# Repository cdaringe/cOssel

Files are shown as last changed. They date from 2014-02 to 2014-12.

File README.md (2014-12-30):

# cOssel
cOssel is a 3D printer.
cOssel makes stuff.
cOssel is big.
cOssel is neat.
cOssel is an iteration of Johann's Kossel. Design intents are equip a dual head end effector and to move the linear rails to an open design. It also uses 20x20 instead of Kossel's 15x15.  Various other design constructs are changed, however, the core design intent of the printer remains.  Default setup includes support for Dual Extruders, heated bed, and EE fan.

## Docs
Please visit the RepRap wiki for docs: http://reprap.org/wiki/COssel

Find printable (RP) files in the /stl folder.  Plates are available in the /stl/plates folder.
Find the official BOM in the root, cossel_BOM.xlsm file.

Adios!  Enjoy!

http://cdaringe.net/

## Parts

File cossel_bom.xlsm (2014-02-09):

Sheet: ExplodedBOM
QtyScalar | ParentLine | . | BOM Level | Part | Qty | UOM | Qty_Exploded | Vendor | Phantom
1 | 1 |  | 0 | (SUPERBOM) | 1 | ea | 1 |  | TRUE
1 | 2 |  | 1 | (post) | 3 | ea | 3 |  | TRUE
3 | 3 |  | 2 | 2020-800mm | 1 | ea | 3 |  | FALSE
3 | 3 |  | 2 | open_rail-700mm | 1 | ea | 3 |  | FALSE
3 | 3 |  | 2 | scrw_m5_10 (open_rail_kit_excess) | 15 | ea | 45 |  | FALSE
3 | 3 |  | 2 | nut_extr_m5 (open_rail_kit_excess) | 15 | ea | 45 |  | FALSE
3 | 3 |  | 2 | rp_base_vertex | 1 | ea | 3 |  | FALSE
3 | 3 |  | 2 | motor_nema_17 | 1 | ea | 3 |  | FALSE
3 | 3 |  | 2 | belt_gt2_1700mm | 1 | ea | 3 |  | FALSE
3 | 3 |  | 2 | gear_drive_belt_gt2 | 1 | ea | 3 |  | FALSE
3 | 3 |  | 2 | scrw_m3_set | 1 | ea | 3 |  | FALSE
3 | 3 |  | 2 | 2020-300mm | 2 | ea | 6 |  | FALSE
3 | 3 |  | 2 | scrw_m4_10 | 8 | ea | 24 |  | FALSE
3 | 3 |  | 2 | wshr_m4 | 10 | ea | 30 |  | FALSE
3 | 3 |  | 2 | nut_m4_extr | 10 | ea | 30 |  | FALSE
3 | 3 |  | 2 | scrw_m3_12 | 4 | ea | 12 |  | FALSE
3 | 3 |  | 2 | wshr_m3 | 4 | ea | 12 |  | FALSE
3 | 3 |  | 2 | scrw_m4_12 | 2 | ea | 6 |  | FALSE
3 | 3 |  | 2 | (carriage) | 1 | ea | 3 |  | TRUE
3 | 20 |  | 3 | rp_plate_slider | 1 | ea | 3 |  | FALSE
3 | 20 |  | 3 | open_rail_shim | 2 | ea | 6 |  | FALSE
3 | 20 |  | 3 | open_rail_wheel_delrin | 2 | ea | 6 |  | FALSE
3 | 20 |  | 3 | open_rail_wheel_sst | 2 | ea | 6 |  | FALSE
3 | 20 |  | 3 | open_rail_bearing | 8 | ea | 24 |  | FALSE
3 | 20 |  | 3 | open_rail_spacer_bearing | 4 | ea | 12 |  | FALSE
3 | 20 |  | 3 | open_rail_shim_eccentric | 2 | ea | 6 |  | FALSE
3 | 20 |  | 3 | open_rail_scrw_m5_std_wheel_mnt | 4 | ea | 12 |  | FALSE
3 | 20 |  | 3 | open_rail_nut_m5 | 4 | ea | 12 |  | FALSE
3 | 20 |  | 3 | rp_flag_carriage | 1 | ea | 3 |  | FALSE
3 | 20 |  | 3 | nut_m3_jam | 3 | ea | 9 |  | FALSE
3 | 20 |  | 3 | wshr_m3 | 3 | ea | 9 |  | FALSE
3 | 20 |  | 3 | nut_m3 | 3 | ea | 9 |  | FALSE
3 | 20 |  | 3 | scrw_m3_20 | 2 | ea | 6 |  | FALSE
1 | 2 |  | 1 | (rods) | 6 | ea | 6 |  | TRUE
6 | 35 |  | 2 | rod_carbon_330mm | 1 | ea | 6 |  | FALSE
6 | 35 |  | 2 | rod_ends | 2 | ea | 12 | klj | FALSE
6 | 35 |  | 2 | scrw_m3_15 | 2 | ea | 12 |  | FALSE
6 | 35 |  | 2 | wshr_m3 | 4 | ea | 24 |  | FALSE
6 | 35 |  | 2 | scrw_m4_set_20 | 2 | ea | 12 |  | FALSE
1 | 2 |  | 1 | (bed) | 1 | ea | 1 |  | TRUE
1 | 41 |  | 2 | pcb_heater | 1 | ea | 1 |  | FALSE
1 | 41 |  | 2 | switch_thermal | 1 | ea | 1 | 150C NC Temperature Switch Ceramic Thermostat KSD301 2 Pcs | FALSE
1 | 41 |  | 2 | scrw_finish_#6 | 1 | ea | 1 |  | FALSE
1 | 41 |  | 2 | bracket_heater_sppt_wood | 1 | ea | 1 |  | FALSE
1 | 41 |  | 2 | bed_glass | 1 | ea | 1 |  | FALSE
1 | 41 |  | 2 | (assy_bed_block) | 3 | ea | 3 |  | TRUE
3 | 47 |  | 3 | scrw_m3_20 | 2 | ea | 6 |  | FALSE
3 | 47 |  | 3 | nut_m3 | 2 | ea | 6 |  | FALSE
3 | 47 |  | 3 | tab_felt | 1 | ea | 3 |  | FALSE
3 | 47 |  | 3 | rp_block_bed | 1 | ea | 3 |  | FALSE
3 | 47 |  | 3 | scrw_m4_12 | 1 | ea | 3 |  | FALSE
3 | 47 |  | 3 | wshr_m4 | 1 | ea | 3 |  | FALSE
3 | 47 |  | 3 | nut_m4_extr | 1 | ea | 3 |  | FALSE
1 | 41 |  | 2 | (kit_bed_install) | 6 | ea | 6 |  | TRUE
6 | 55 |  | 3 | wshr_m4 | 3 | ea | 18 |  | FALSE
6 | 55 |  | 3 | scrw_m4_15 | 1 | ea | 6 |  | FALSE
6 | 55 |  | 3 | spring_m4 | 1 | ea | 6 | http://www.homedepot.com/p/Everbilt-Spring-Assortment-Kit-84-Pack-15642/202045461 | FALSE
6 | 55 |  | 3 | nut_m4_extr | 1 | ea | 6 |  | FALSE
1 | 2 |  | 1 | (post_top) | 3 | ea | 3 |  | TRUE
3 | 60 |  | 2 | rp_upper_vertex | 1 | ea | 3 |  | FALSE
3 | 60 |  | 2 | 2020-371mm | 1 | ea | 3 |  | FALSE
3 | 60 |  | 2 | nut_m4_extr | 4 | ea | 12 |  | FALSE
3 | 60 |  | 2 | scrw_m4_15 | 4 | ea | 12 |  | FALSE
3 | 60 |  | 2 | wshr_m4 | 8 | ea | 24 |  | FALSE
3 | 60 |  | 2 | wshr_m4_fender | 1 | ea | 3 |  | FALSE
3 | 60 |  | 2 | nut_m4 | 1 | ea | 3 |  | FALSE
3 | 60 |  | 2 | bearing_624z | 2 | ea | 6 |  | FALSE
3 | 60 |  | 2 | scrw_m4_25 | 1 | ea | 3 |  | FALSE
3 | 60 |  | 2 | scrw_m4_12 | 1 | ea | 3 |  | FALSE
3 | 60 |  | 2 | (assy_opto) | 1 | ea | 3 |  | TRUE
3 | 71 |  | 3 | rp_opto_mount | 1 | ea | 3 |  | FALSE
3 | 71 |  | 3 | open_rail_shim | 1 | ea | 3 |  | FALSE
3 | 71 |  | 3 | scrw_m4_15 | 1 | ea | 3 |  | FALSE
3 | 71 |  | 3 | nut_m4_extr | 1 | ea | 3 |  | FALSE
3 | 71 |  | 3 | wshr_m4_fender | 1 | ea | 3 |  | FALSE
3 | 71 |  | 3 | wshr_m4 | 1 | ea | 3 |  | FALSE
3 | 71 |  | 3 | wshr_m4 | 1 | ea | 3 |  | FALSE
3 | 71 |  | 3 | scrw_m3_12 | 2 | ea | 6 |  | FALSE
3 | 71 |  | 3 | wshr_m3 | 4 | ea | 12 |  | FALSE
3 | 71 |  | 3 | nut_m3 | 2 | ea | 6 |  | FALSE
3 | 71 |  | 3 | pcb_opto | 1 | ea | 3 |  | FALSE
1 | 2 |  | 1 | (assy_pwr_spply) | 1 | ea | 1 |  | TRUE
1 | 83 |  | 2 | power_supply | 1 | ea | 1 |  | FALSE
1 | 83 |  | 2 | rp_bracket_pwr_spply_tab | 2 | ea | 2 |  | FALSE
1 | 83 |  | 2 | bracket_power_supply_stablity_xy | 1 | ea | 1 |  | FALSE
1 | 83 |  | 2 | scrw_m4_10 | 5 | ea | 5 |  | FALSE
1 | 83 |  | 2 | nut_m4_extr | 5 | ea | 5 |  | FALSE
1 | 83 |  | 2 | wshr_m4 | 5 | ea | 5 |  | FALSE
1 | 2 |  | 1 | (kit_spool_extruder_mount_framing) | 1 | ea | 1 |  | TRUE
1 | 90 |  | 2 | bracket_tee_2020 | 9 | ea | 9 |  | FALSE
1 | 90 |  | 2 | nut_extr_m5 (open_rail_kit_excess) | 18 | ea | 18 |  | FALSE
1 | 90 |  | 2 | scrw_m5_10 (open_rail_kit_excess) | 18 | ea | 18 |  | FALSE
1 | 90 |  | 2 | 2020-200mm | 3 | ea | 3 |  | FALSE
1 | 90 |  | 2 | 2020-300mm | 1 | ea | 1 |  | FALSE
1 | 90 |  | 2 | 2020-50mm | 2 | ea | 2 |  | FALSE
1 | 90 |  | 2 | 2020-134mm | 1 | ea | 1 |  | FALSE
1 | 90 |  | 2 | rp_extruder_join_upper | 1 | ea | 1 |  | FALSE
1 | 90 |  | 2 | rp_extruder_join_lower | 1 | ea | 1 |  | FALSE
1 | 90 |  | 2 | wshr_m4 | 4 | ea | 4 |  | FALSE
1 | 90 |  | 2 | scrw_m4_10 | 4 | ea | 4 |  | FALSE

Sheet: FlatBOM
Phantom | FALSE
Part | Total Qty | Vendor | MFG PN | Vendor PN | Notes | URL
2020_cap | 16 | Misumi | HFC5-2020 | HFC5-2020 | Site is designed for commerical customers, but you can still setup an account. You must manually enter the part numbers into a purchase order. | [http://us.misumi-ec.com/]
2020-134mm | 1 | Misumi | HFS5-2020-134 | HFS5-2020-134 | Site is designed for commerical customers, but you can still setup an account. You must manually enter the part numbers into a purchase order. | [http://us.misumi-ec.com/]
2020-200mm | 3 | Misumi | HFS5-2020-200 | HFS5-2020-200 | Site is designed for commerical customers, but you can still setup an account. You must manually enter the part numbers into a purchase order. | [http://us.misumi-ec.com/]
2020-300mm | 7 | Misumi | HFS5-2020-300 | HFS5-2020-300 | Site is designed for commerical customers, but you can still setup an account. You must manually enter the part numbers into a purchase order. | [http://us.misumi-ec.com/]
2020-371mm | 7 | Misumi | HFS5-2020-371 | HFS5-2020-371 | Site is designed for commerical customers, but you can still setup an account. You must manually enter the part numbers into a purchase order. | [http://us.misumi-ec.com/]
2020-50mm | 2 | Misumi | HFS5-2020-50 | HFS5-2020-50 | Site is designed for commerical customers, but you can still setup an account. You must manually enter the part numbers into a purchase order. | [http://us.misumi-ec.com/]
2020-800mm | 3 | Misumi | HFS5-2020-800 | HFS5-2020-800 | Site is designed for commerical customers, but you can still setup an account. You must manually enter the part numbers into a purchase order. | [http://us.misumi-ec.com/]
bearing_608z | 4 | Amazon | 608z |  | Easily sourced | [http://www.amazon.com/Amico-Single-Shielded-Miniature-Bearings/dp/B00843OUNI
bearing_624z | 6 | Amazon | 624z |  | Easily sourced | [http://www.amazon.com/Amico-Single-Shielded-Groove-Bearing/dp/B00AUB7M3C
bed_glass | 1 | SeeMeCNC |  | 26602 | 300mm, round borosilicate! | [http://seemecnc.com/products/boroscillicate-glass-build-plate-300mm]
belt_gt2_1700mm | 3 | OpenBuilds |  |  | Order by the foot. 304.8 mm / ft! | [http://openbuildspartstore.com/gt2-2mm-timing-belt/]
brace_frame | 6 | Ponoko |  |  | Legacy brace. Still may be viable and desired by some users. Included by default in Ponoko cut-out .svg | [http://www.ponoko.com/design-your-own/products/cossel-wood-plate-11227]
brace_spacer | 12 | Ponoko |  |  | Legacy brace. Still may be viable and desired by some users. Included by default in Ponoko cut-out .svg | [http://www.ponoko.com/design-your-own/products/cossel-wood-plate-11227]
bracket_heater_sppt_wood | 1 | Ponoko |  |  | Wooden piece. Laser cutting files on GitHub & ponoko | [http://www.ponoko.com/design-your-own/products/cossel-wood-plate-11227]
bracket_hot_end_groovemount_dual | 1 | Ponoko |  |  | Wooden piece. Laser cutting files on GitHub & ponoko | [http://www.ponoko.com/design-your-own/products/cossel-wood-plate-11227]
bracket_power_supply_stablity_xy | 1 | Ponoko |  |  | Wooden piece. Laser cutting files on GitHub & ponoko | [http://www.ponoko.com/design-your-own/products/cossel-wood-plate-11227]
bracket_tee_2020 | 9 | Misumui | HBLFSN5 | HBLFSN5 | Site is designed for commerical customers, but you can still setup an account. You must manually enter the part numbers into a purchase order. | [http://us.misumi-ec.com/]
cable_ribbon_10_conductor_15ft | 2 | SparkFun |  | CAB-1064 | Used for bulk-running the opto +V, SIG, & GND to the board. Also used for clean motor runs and I/O to the EE. Note, some have suggested this is too thin of wire gauge. User to decide | [https://www.sparkfun.com/products/10647]
drive_filament_dia | 2 | RepRap Sources |  |  | Mk7-like with 8mm bore to be compatible with phidgets geared steppers. | [http://reprap.org/wiki/Drive-gear]
epoxy_two_part | 1 | Amazon |  |  | For gluing the rod ends to the carbon tubing | [http://www.amazon.com/Devcon-2-Ton-Crystal-Clear-0-84-Ounce/dp/B0006O8QQ0?s=toys-and-games
extruder_maker_gear | 2 | MakerGear |  |  | Make sure to configure your order for 1.75 barrel. | [http://www.makergear.com/products/extruders]
fan_40mm_12VDC | 2 | Amazon |  |  | Most 40mm 12VDC fans should do the trick | [http://www.amazon.com/Gelid-Solutions-Silent-40mm-FN-SX04-42/dp/B00BF3S83C?s=electronics
fitting_one_touch_4mm | 4 | Amazon | KQ2S04-M5A |  | 5mm thread req'd and 4mm OD tube receptable req'd | [http://www.amazon.com/dp/B00AM42V6U/ref=biss_dp_sa1]
gear_drive_belt_gt2 | 3 | OpenBuilds |  |  | 20 tooth or less is critical to prevent the belt from hitting the carriage | [http://openbuildspartstore.com/gt2-2mm-aluminum-timing-pulley-20/]
motor_nema_17 | 3 | Ultimachine |  | UMN17MTR | Std reprap motor | [https://ultimachine.com/content/kysan-1124090-nema-17-stepper-motor]
motor_nema_17_geared_5.18_1 | 2 | Phidgets |  | 3317_1 | Extra torque required for long bowden path to hot end | [http://www.phidgets.com/products.php?product_id=3317]
nut_extr_m5 (open_rail_kit_excess) | 69 | OpenBuilds |  |  | Do not order directly for hardware. You will have excess from your wheel kits which instead use the eccentric spacer.
nut_m3 | 35 | Fastenal |  |  | Nylon lock preferred | [http://www.fastenal.com/web/products/details/1L2510000A20000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]
nut_m3_jam | 13 | Fastenal |  |  | Jam | [http://www.fastenal.com/web/products/details/MJ2510000A20000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]
nut_m4 | 20 | Fastenal |  |  | Nylon lock preferred | [http://www.fastenal.com/web/products/details/1L2530000A20000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]
nut_m4_extr | 91 | Misumi | HNTTBS5-4 | HNTTBS5-4 | Site is designed for commerical customers, but you can still setup an account. You must manually enter the part numbers into a purchase order.
open_rail_bearing | 24 | OpenBuilds |  |  | Do not order directly for hardware. You will have excess from your wheel kits which instead use the eccentric spacer.
open_rail_nut_m5 | 14 | OpenBuilds |  |  | Do not order directly for hardware. You will have excess from your wheel kits which instead use the eccentric spacer.
open_rail_scrw_m5_std_wheel_mnt | 12 | OpenBuilds |  |  | Do not order directly for hardware. You will have excess from your wheel kits which instead use the eccentric spacer.
open_rail_shim | 9 | OpenBuilds |  |  | Do not order directly for hardware. You will have excess from your wheel kits which instead use the eccentric spacer.
open_rail_shim_eccentric | 6 | OpenBuilds |  |  | Stock availability can be shaky. May need to adapt a different eccentric nut. | [http://openbuildspartstore.com/eccentric-spacers/]
open_rail_spacer_bearing | 12 | OpenBuilds |  |  | Do not order directly for hardware. You will have excess from your wheel kits which instead use the eccentric spacer.
open_rail_wheel_delrin | 6 | OpenBuilds |  |  | Wheel kit | [http://openbuildspartstore.com/openbuilds-dual-v-wheel-kit-delrin/]
open_rail_wheel_sst | 6 | OpenBuilds |  |  | Wheel kit | [http://openbuildspartstore.com/openbuilds-dual-v-wheel-kit-metal/]
open_rail-700mm | 3 | OpenBuilds |  |  | Order the 1000mm's and cut to length | [http://openbuildspartstore.com/openrail-black-anodized/]
pcb_arduino_mega | 1 | Ultimachine |  |  | Note: The RAMPS stack below includes a MEGA 2560. Make sure not to double buy! | [https://ultimachine.com/content/arduino-mega-2560-r3]
pcb_fan_extension_board | 1 | Geeetech |  |  | Or make your own! [http://cdaringe.net/blurb/cossel-fan-extension-board/ cdaringe opto-extension board] | [http://www.geeetech.com/wiki/index.php/Reprap_Ramps1.4_RRD_Fan_Extender]
pcb_heater | 1 | Ultimachine |  |  | Prusa Heater | [https://ultimachine.com/content/prusa-pcb-heated-bed]
pcb_opto | 3 | Ultimachine |  |  | Std opto's | [https://ultimachine.com/oek]
pcb_RAMPS_stack | 1 | Ultimachine |  |  | Single Z, not dual Z configuration. | [https://ultimachine.com/ramps-pre-assembled-kit-complete]
pcb_sd_ramps_extension_board | 1 | Geeetech |  |  | Strongly recommended as pausing issues occur when printing via USB | [http://www.geeetech.com/wiki/index.php/SD_for_RAMPS]
power_supply | 1 | Thermaltake | TR2 TR-700 | N82E16817153167 | ATX PS. Quiet, reliable. | [http://www.newegg.com/Product/Product.aspx?Item=N82E16817153167]
rod_carbon_330mm | 6 | Hobby-Lobby |  | GXT5540 | Must be cut to size. 3x 1000 rods will satisfy a std build | [http://www.hobbyexpress.com/carbon_fiber_tube_5.5_x_4.0_x_1000_mm_24247_prd1.htm?pSearchQueryId=4680220]
rod_ends | 12 | Amazon | 5347 |  | 4mm OD receptable, 3mm thru-hole ball-ends | [http://www.amazon.com/Traxxas-5347-Hollow-Balls-Large/dp/B000BOLVJY]
rod_threaded_8mm-271mm | 1 | Grainger |  |  | 5/16" rod is ~8mm too. You can buy 5/16" rod at hardware stores (i.e. Home Depot) for a couple of bucks. | [http://reprap.org/wiki/Threaded_rod]
rp_base_vertex | 3 | RP | RP | RP | Files on GitHub | [https://github.com/cdaringe/cOssel/tree/master/stl]
rp_block_bed | 3 | RP | RP | RP | Files on GitHub | [https://github.com/cdaringe/cOssel/tree/master/stl]
rp_brace_top_vertex | 3 | RP | RP | RP | Files on GitHub | [https://github.com/cdaringe/cOssel/tree/master/stl]
rp_bracket_axle_spool | 3 | RP | RP | RP | Files on GitHub | [https://github.com/cdaringe/cOssel/tree/master/stl]
rp_bracket_lateral_sppt | 4 | RP | RP | RP | Files on GitHub | [https://github.com/cdaringe/cOssel/tree/master/stl]
rp_bracket_lateral_sppt_mirrored | 4 | RP | RP | RP | Files on GitHub | [https://github.com/cdaringe/cOssel/tree/master/stl]
rp_bracket_pwr_spply_tab | 2 | RP | RP | RP | Files on GitHub | [https://github.com/cdaringe/cOssel/tree/master/stl]
rp_bracket_RAMPS | 1 | RP | RP | RP | Files on GitHub | [https://github.com/cdaringe/cOssel/tree/master/stl]
rp_end_effector | 1 | RP | RP | RP | Files on GitHub | [https://github.com/cdaringe/cOssel/tree/master/stl]
rp_extruder_cossel_bowden_mirrored | 2 | RP | RP | RP | Files on GitHub | [https://github.com/cdaringe/cOssel/tree/master/stl]
rp_extruder_join_lower | 1 | RP | RP | RP | Files on GitHub | [https://github.com/cdaringe/cOssel/tree/master/stl]
rp_extruder_join_upper | 1 | RP | RP | RP | Files on GitHub | [https://github.com/cdaringe/cOssel/tree/master/stl]
rp_flag_carriage | 3 | RP | RP | RP | Files on GitHub | [https://github.com/cdaringe/cOssel/tree/master/stl]
rp_idler | 1 | RP | RP | RP | Files on GitHub | [https://github.com/cdaringe/cOssel/tree/master/stl]
rp_idler_boss_bearing_8mm | 2 | RP | RP | RP | Files on GitHub | [https://github.com/cdaringe/cOssel/tree/master/stl]
rp_idler_mirrored | 1 | RP | RP | RP | Files on GitHub | [https://github.com/cdaringe/cOssel/tree/master/stl]
rp_idler_strut | 2 | RP | RP | RP | Files on GitHub | [https://github.com/cdaringe/cOssel/tree/master/stl]
rp_mount_fan_ee | 1 | RP | RP | RP | Files on GitHub | [https://github.com/cdaringe/cOssel/tree/master/stl]
rp_mount_fan_motor_drivers | 1 | RP | RP | RP | Files on GitHub | [https://github.com/cdaringe/cOssel/tree/master/stl]
rp_opto_mount | 3 | RP | RP | RP | Files on GitHub | [https://github.com/cdaringe/cOssel/tree/master/stl]
rp_plate_slider | 3 | RP | RP | RP | Files on GitHub | [https://github.com/cdaringe/cOssel/tree/master/stl]
rp_upper_vertex | 3 | RP | RP | RP | Files on GitHub | [https://github.com/cdaringe/cOssel/tree/master/stl]
scrw_finish_#6 | 1 | Fastenal |  |  | Thermal switch is not required, but strongly recommended for safety
scrw_m3_10 | 8 | Fastenal |  |  | Pan head & SST preferred when applicable.
scrw_m3_12 | 18 | Fastenal |  |  | Pan head & SST preferred when applicable.
scrw_m3_15 | 14 | Fastenal |  |  | Pan head & SST preferred when applicable.
scrw_m3_20 | 17 | Fastenal |  |  | Pan head & SST preferred when applicable.
scrw_m3_25 | 2 | Fastenal |  |  | Pan head & SST preferred when applicable.
scrw_m3_35 | 2 | Fastenal |  |  | Pan head & SST preferred when applicable.
scrw_m3_50 | 4 | Fastenal |  |  | Pan head & SST preferred when applicable.
scrw_m3_set | 5 | Fastenal |  |  | Only order this if your timing pulleys and filament drive gear do not come with their own. They nearly always do.
scrw_m4_10 | 47 | Fastenal |  |  | Pan head & SST preferred when applicable.
scrw_m4_12 | 30 | Fastenal |  |  | Pan head & SST preferred when applicable.
scrw_m4_15 | 25 | Fastenal |  |  | Pan head & SST preferred when applicable.
scrw_m4_20 | 12 | Fastenal |  |  | Pan head & SST preferred when applicable.
scrw_m4_25 | 4 | Fastenal |  |  | Pan head & SST preferred when applicable.
scrw_m4_8 | 22 | Fastenal |  |  | Pan head & SST preferred when applicable.
scrw_m4_set_20 | 12 | Fastenal |  |  | Rod End Mounts | [http://www.fastenal.com/web/products/details/MX2530020A20000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]
scrw_m5_10 (open_rail_kit_excess) | 67 | OpenBuilds |  |  | Do not order directly for hardware. Hardware comes kitted with your rail. | [http://openbuildspartstore.com/openrail-black-anodized/]
spring_m3_extruder | 4 | Home Depot |  |  | Only 1x spring kit reqd | [http://www.homedepot.com/p/Everbilt-Spring-Assortment-Kit-84-Pack-15642/202045461]
spring_m4 | 7 | Home Depot |  |  | Only 1x spring kit reqd | [http://www.homedepot.com/p/Everbilt-Spring-Assortment-Kit-84-Pack-15642/202045461]
switch_thermal | 1 | Amazon | Amico KSD301 |  | Recommended for safety | [http://www.amazon.com/Amico-Thermostat-Temperature-Control-Celsius/dp/B007Q81IQY]
tab_felt | 3 | (no vendor data entered) |  |  | This is a thermal barrier between the bed and the bed clamp. Simply household cloth shall suffice.
tubing_4mm_bowden_1000mm | 2 | MakerShop |  |  | Any common RepRap 4mm tube shall suffice | [http://www.makershop.co.nz/PFA_4-2MM]
wire_raceway_10in | 1 | McMaster-Carr |  | 7578K73 | The 6'6" is enough for your full build | [http://www.mcmaster.com/#catalog/120/862/=qly4to]
wire_raceway_25in | 1 | McMaster-Carr |  | 7578K73 | The 6'6" is enough for your full build | [http://www.mcmaster.com/#catalog/120/862/=qly4to]
wire_raceway_5in | 2 | McMaster-Carr |  | 7578K73 | The 6'6" is enough for your full build | [http://www.mcmaster.com/#catalog/120/862/=qly4to]
wire_raceway_8in | 1 | McMaster-Carr |  | 7578K73 | The 6'6" is enough for your full build | [http://www.mcmaster.com/#catalog/120/862/=qly4to]
wire_wrap_10ft | 1 | McMaster-Carr |  | 7378K41 | Pick a color! You may use 8+ ft. | [http://www.mcmaster.com/#spiral-bundling-wrap/=qm0474]
wshr_4mm | 8 | Fastenal |  |  | SST preferred
wshr_m3 | 69 | Fastenal |  |  | SST preferred
wshr_m4 | 145 | Fastenal |  |  | SST preferred
wshr_m4_fender | 6 | Fastenal |  |  | SST preferred | [http://www.fastenal.com/web/products/details/11511778?isPunchout=false]
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

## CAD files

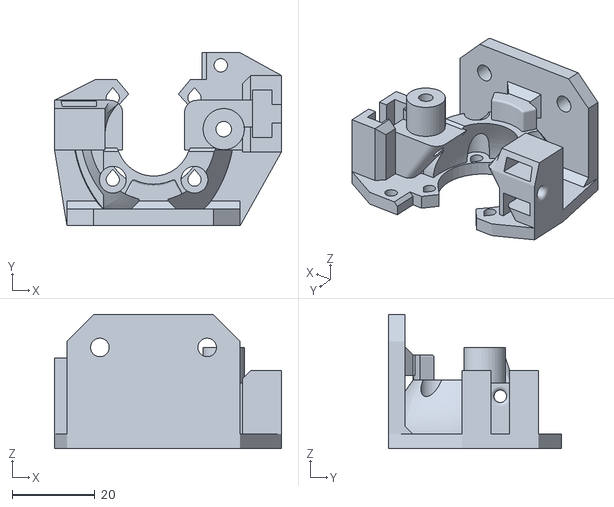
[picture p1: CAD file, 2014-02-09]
cad/extruder/rp_extruder_cossel_bowden_mirrored.STL
55.0 x 42.0 x 32.5

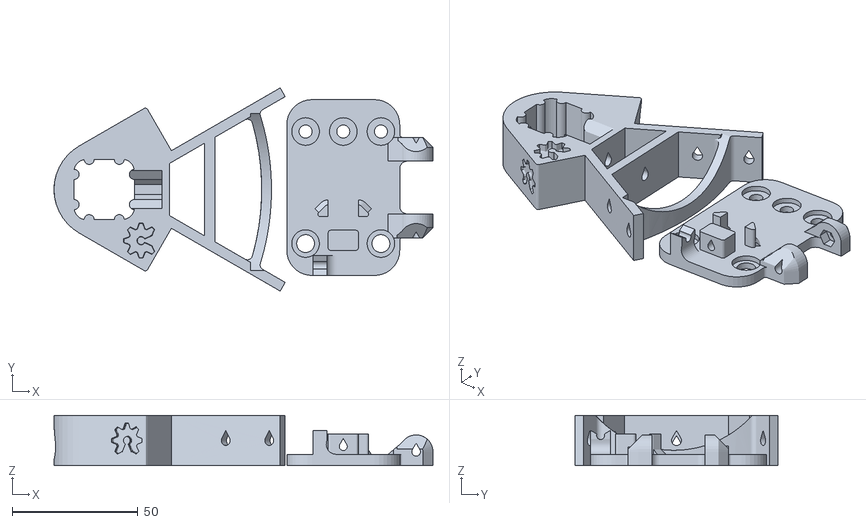
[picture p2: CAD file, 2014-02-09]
cad/plate/tray_B_3x.stl
150.9 x 80.9 x 20.0

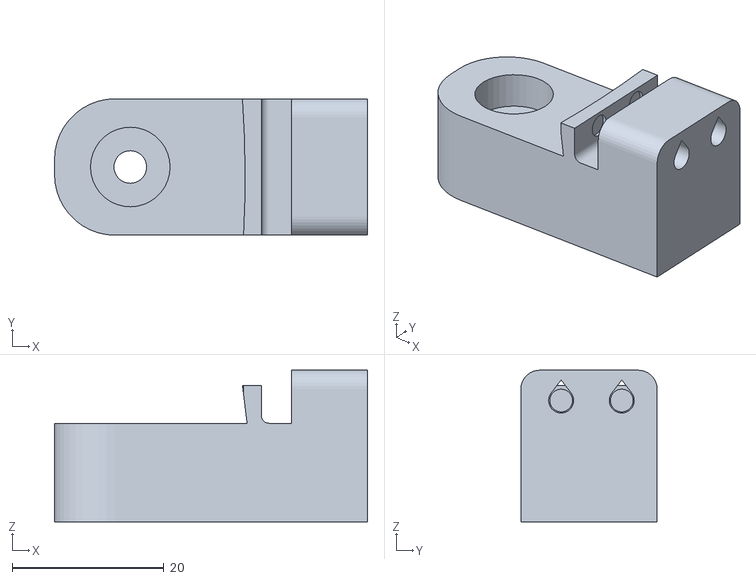
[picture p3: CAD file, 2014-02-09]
cad/rp_block_bed.STL
41.3 x 18.0 x 20.0

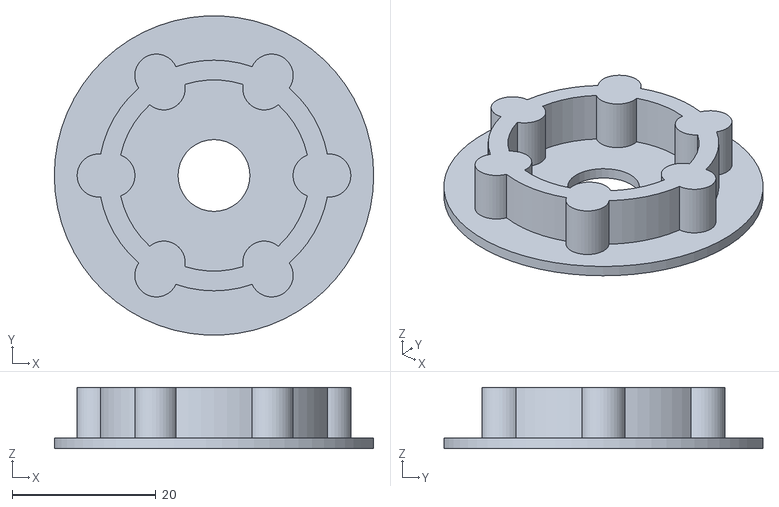
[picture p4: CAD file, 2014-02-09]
cad/spool/rp_spool_axle_small_OD_makergeeks.stl
44.5 x 44.4 x 8.50

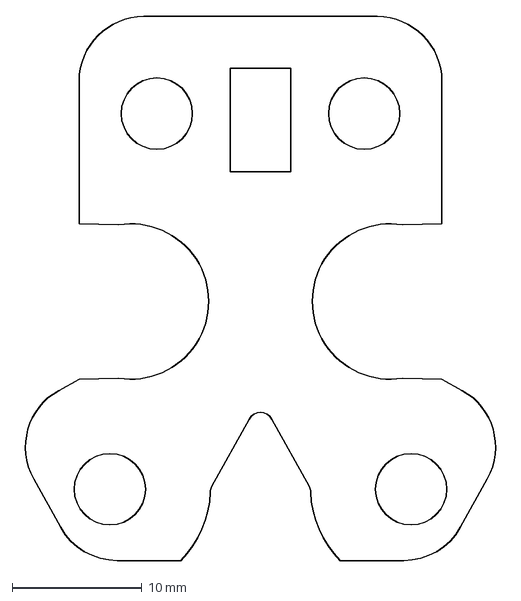
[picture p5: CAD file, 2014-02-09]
drw/laser/bracket_groove_mount_dual_he.DXF
37.7 x 42.0 mm

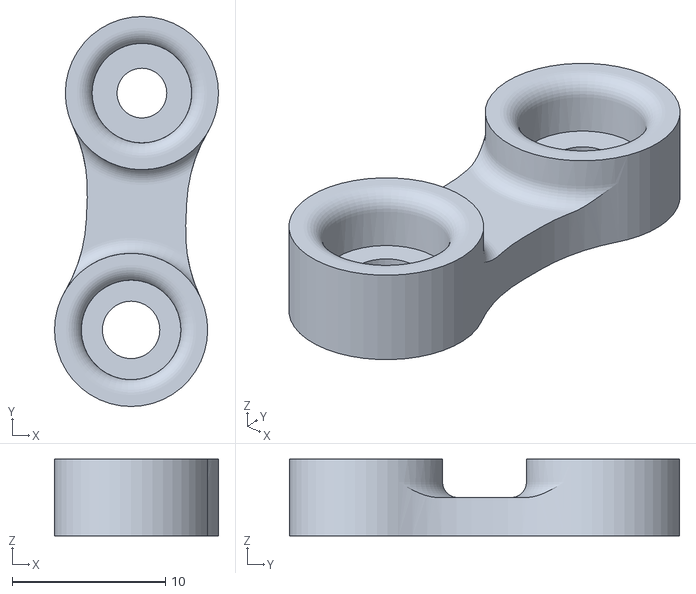
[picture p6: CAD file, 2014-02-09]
cad/extruder/rp_idler_strut.STL
10.7 x 25.5 x 5.00

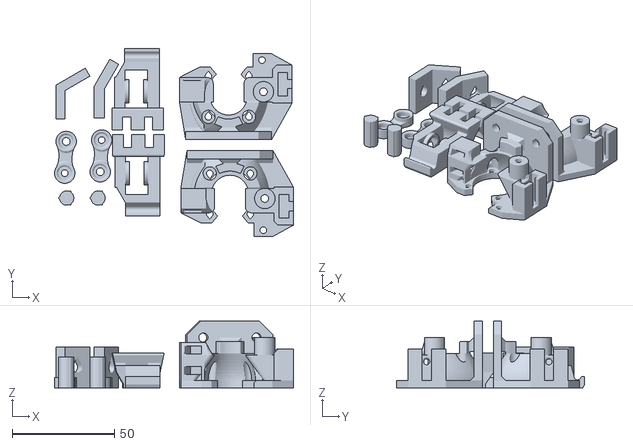
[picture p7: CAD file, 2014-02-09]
cad/plate/tray_D_1x.stl
116.7 x 91.9 x 32.5

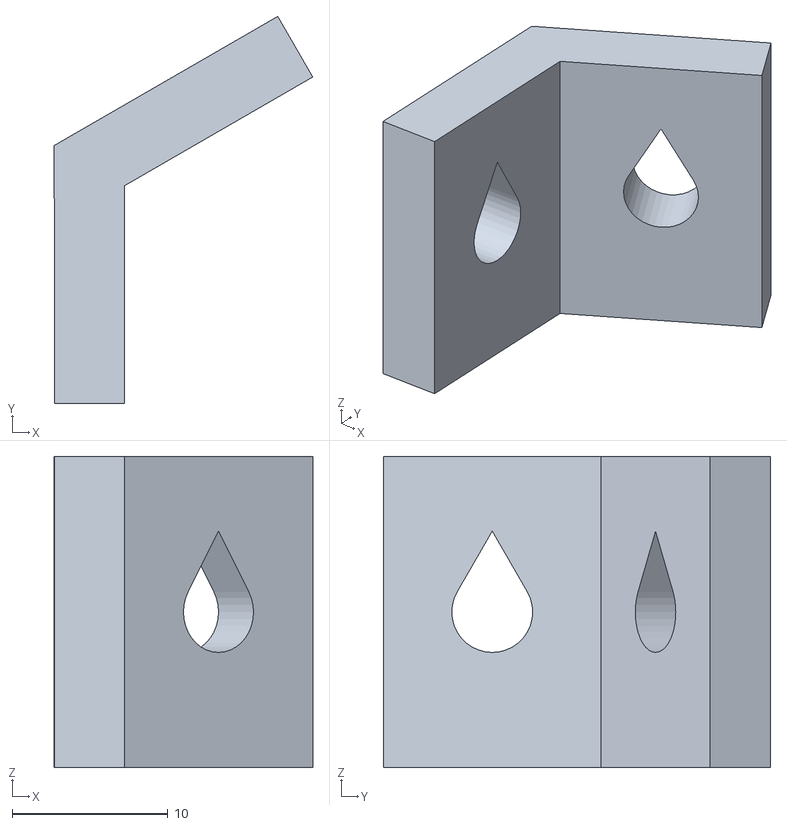
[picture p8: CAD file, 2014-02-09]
cad/rp_extruder_join_lower.STL
16.6 x 24.9 x 20.0

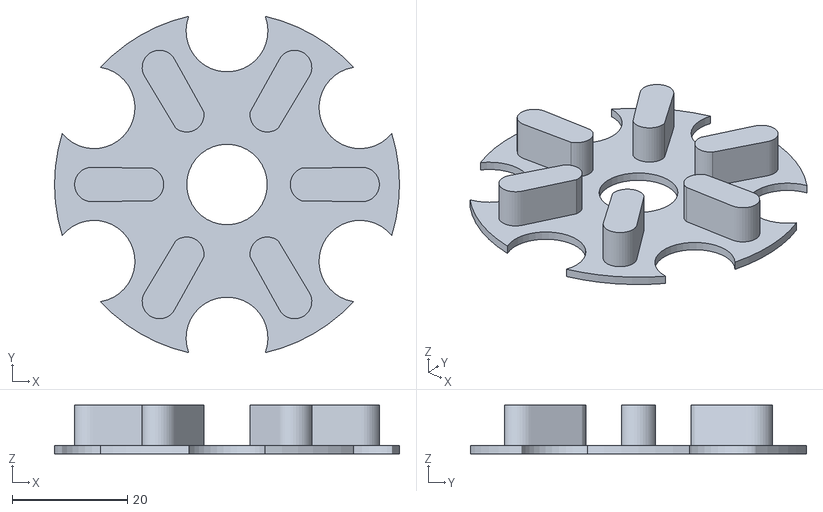
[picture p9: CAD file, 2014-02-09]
cad/spool/rp_spool_axle_large_OD_makergeeks.STL
60.0 x 58.5 x 8.50

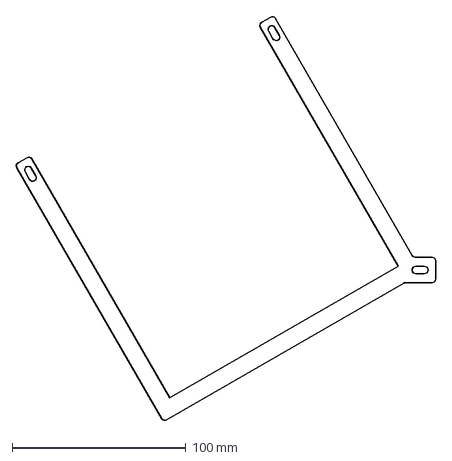
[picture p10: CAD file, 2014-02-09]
drw/laser/bracket_power_supply_stablity_xy.DXF
241.7 x 233.2 mm

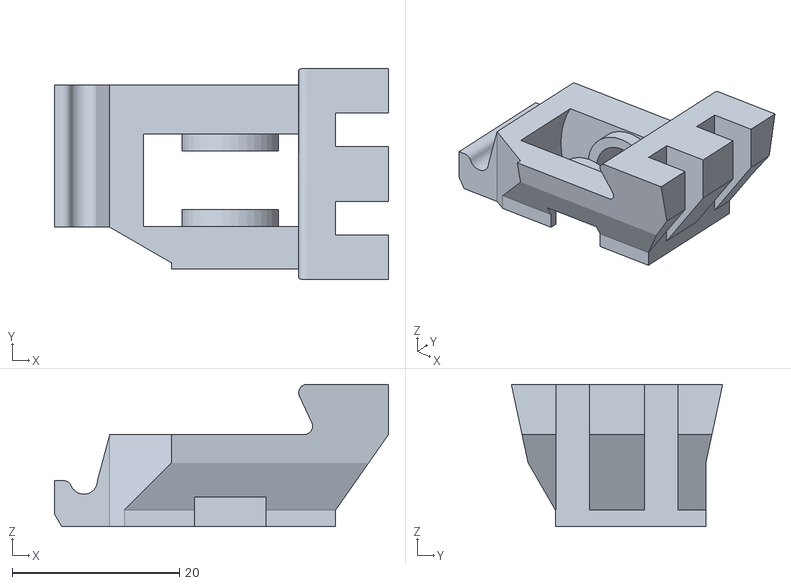
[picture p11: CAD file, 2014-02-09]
cad/extruder/rp_idler_mirrored.STL
39.9 x 25.2 x 17.0

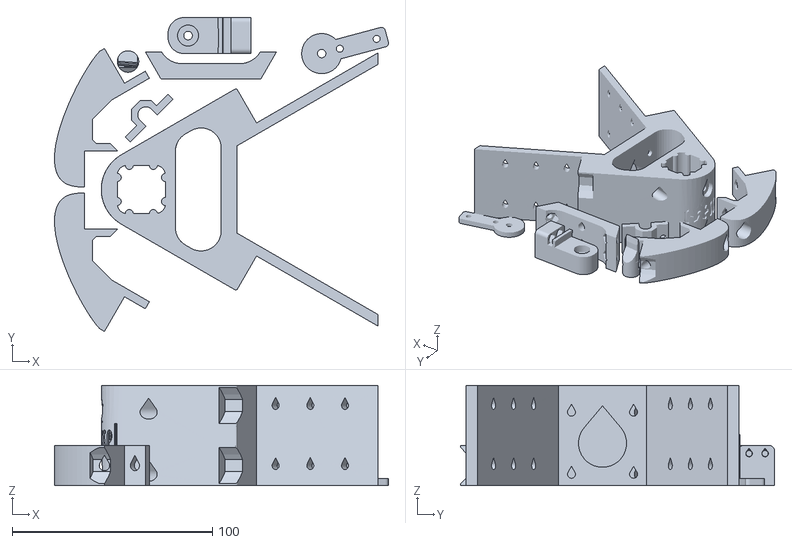
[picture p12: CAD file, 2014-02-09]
cad/plate/tray_A_3x.stl
166.7 x 156.7 x 50.0

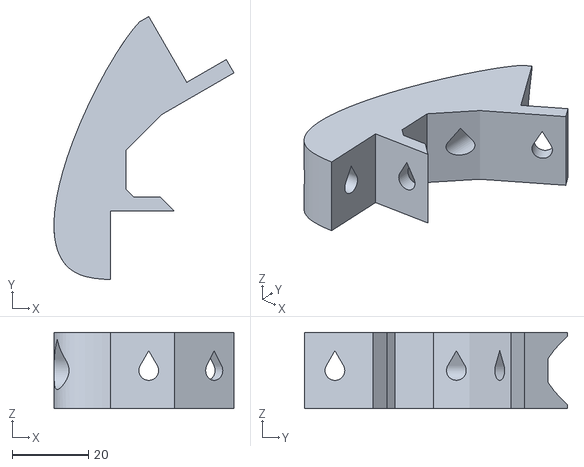
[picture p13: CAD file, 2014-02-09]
cad/rp_bracket_lateral_sppt.STL
47.4 x 69.2 x 20.0

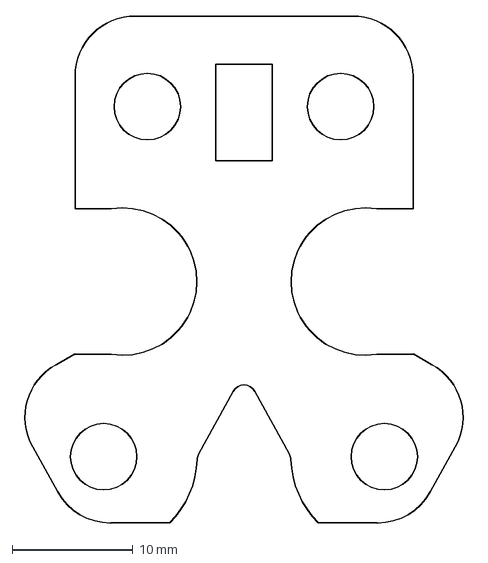
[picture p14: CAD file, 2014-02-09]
drw/laser/bracket_groove_mount_dual_he_slop.DXF
37.7 x 42.0 mm

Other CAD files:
cad/extruder/rp_extruder_cossel_bowden.STL
cad/plate/tray_C_1x.stl
drw/laser/bracket_heater_sppt_wood.DXF
cad/extruder/rp_idler.STL
cad/extruder/rp_idler_boss_bearing_8mm.STL
cad/legacy/bracket_depth_gauge.STL
cad/legacy/bracket_snsr.STL
cad/legacy/bracket_snsr_r4.STL
cad/legacy/end_effector.STL
cad/legacy/filament_guide.STL
cad/rp_base_vertex_OP1_no_nut_slots.stl
cad/rp_base_vertex_OP2_nut_slots.STL
cad/rp_brace_top_vertex.STL
cad/rp_bracket_RAMPS.STL
cad/rp_bracket_axle_spool.STL
cad/rp_bracket_lateral_sppt_mirrored.STL
cad/rp_bracket_pwr_spply_tab.stl
cad/rp_end_effector.STL
cad/rp_extruder_join_upper.STL
cad/rp_flag_carriage.STL
cad/rp_mount_fan_ee.STL
cad/rp_mount_fan_motor_drivers.STL
cad/rp_opto_mount.STL
cad/rp_plate_slider.STL
cad/rp_upper_vertex_OP1_no_nut_slots.STL
cad/rp_upper_vertex_OP2_nut_slots.STL

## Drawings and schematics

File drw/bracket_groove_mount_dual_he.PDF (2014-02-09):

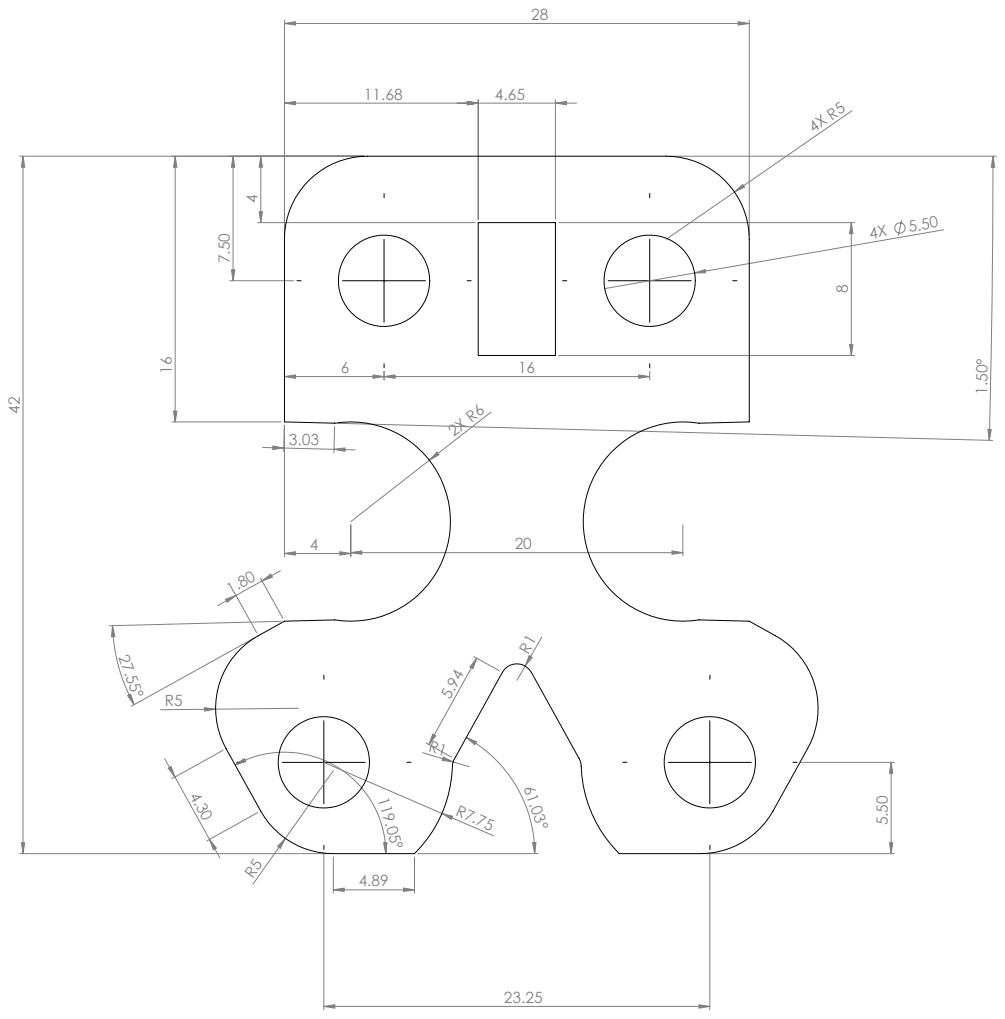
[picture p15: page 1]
SCALE:5:1; SHEET 1 OF 1; DO NOT SCALE DRAWING; REVISION; DEBUR AND BREAK SHARP; UNLESS OTHERWISE SPECIFIED:; FINISH:

DIMENSIONS ARE IN MILLIMETERS
SURFACE FINISH:
TOLERANCES:
LINEAR:
ANGULAR:

NAME | SIGNATURE | DATE | | | | TITLE:
Q.A | | | | MATERIAL: bracket_groove_mount_dual_he WEIGHT: | DWG NO. | A1

DRAWN
CHK'D
APPV'D
MFG

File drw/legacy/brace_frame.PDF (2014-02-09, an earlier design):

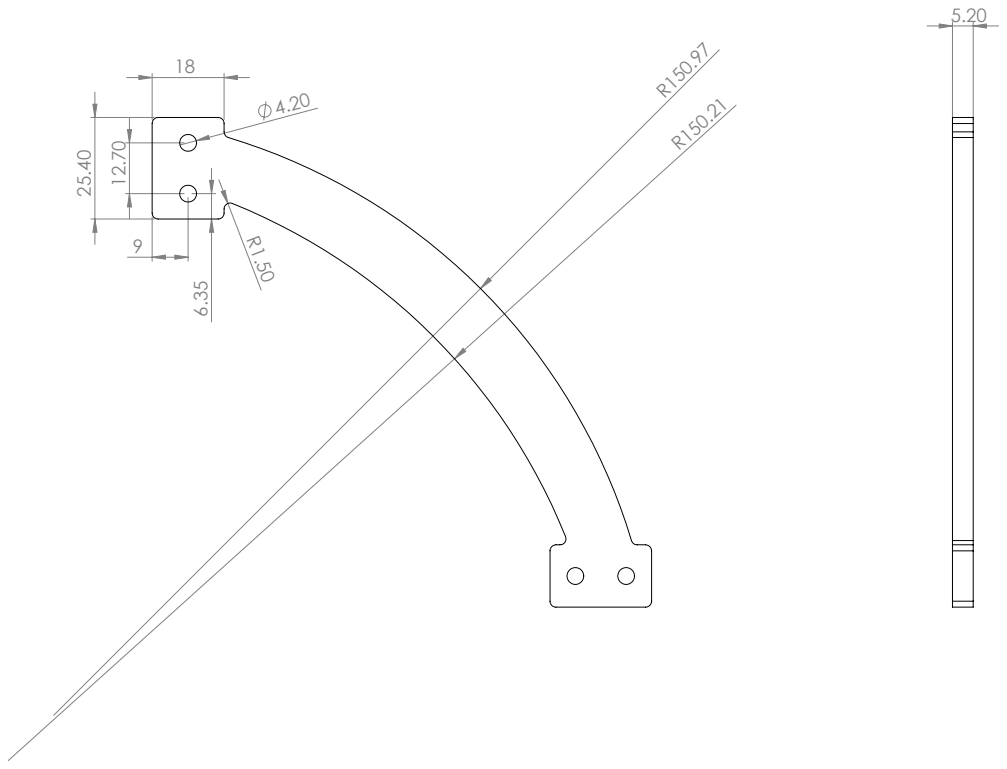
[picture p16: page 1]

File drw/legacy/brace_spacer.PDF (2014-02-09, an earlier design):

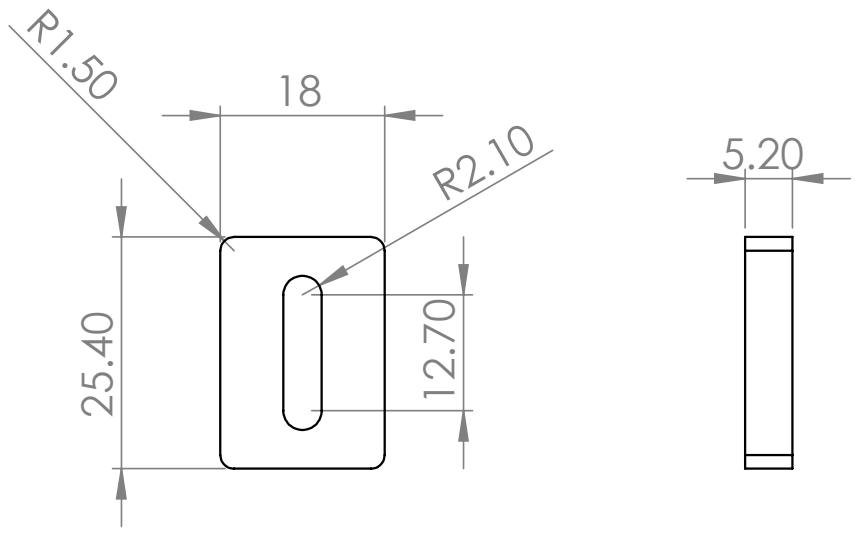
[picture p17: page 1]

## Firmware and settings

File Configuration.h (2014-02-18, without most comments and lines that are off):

#define CONFIGURATION_H
#define STRING_VERSION_CONFIG_H __DATE__ " " __TIME__ // build date and time
#define STRING_CONFIG_H_AUTHOR "(cdaringe, cOssel)" // Who made the changes.
#define SERIAL_PORT 0
#define BAUDRATE 115200
#define MOTHERBOARD 33
#define EXTRUDERS 2
#define POWER_SUPPLY 1
#define DELTA
#define DELTA_SEGMENTS_PER_SECOND 200
#define DELTA_DIAGONAL_ROD 215.0 // mm
#define DELTA_SMOOTH_ROD_OFFSET 137.0 // mm
#define DELTA_EFFECTOR_OFFSET 19.9 // mm
#define DELTA_CARRIAGE_OFFSET 19.5 // mm
#define DELTA_RADIUS (DELTA_SMOOTH_ROD_OFFSET-DELTA_EFFECTOR_OFFSET-DELTA_CARRIAGE_OFFSET)
#define SIN_60 0.8660254037844386
#define COS_60 0.5
#define DELTA_TOWER1_X -SIN_60*DELTA_RADIUS // front left tower
#define DELTA_TOWER1_Y -COS_60*DELTA_RADIUS
#define DELTA_TOWER2_X SIN_60*DELTA_RADIUS // front right tower
#define DELTA_TOWER2_Y -COS_60*DELTA_RADIUS
#define DELTA_TOWER3_X 0.0 // back middle tower
#define DELTA_TOWER3_Y DELTA_RADIUS
#define DELTA_DIAGONAL_ROD_2 pow(DELTA_DIAGONAL_ROD,2)
#define TEMP_SENSOR_0 5
#define TEMP_SENSOR_1 0
#define TEMP_SENSOR_2 0
#define TEMP_SENSOR_BED 0
#define MAX_REDUNDANT_TEMP_SENSOR_DIFF 10
#define TEMP_RESIDENCY_TIME 10  // (seconds)
#define TEMP_HYSTERESIS 3       // (degC) range of +/- temperatures considered "close" to the target one
#define TEMP_WINDOW     1       // (degC) Window around target to start the residency timer x degC early.
#define HEATER_0_MINTEMP 5
#define HEATER_1_MINTEMP 5
#define HEATER_2_MINTEMP 5
#define BED_MINTEMP 5
#define HEATER_0_MAXTEMP 275
#define HEATER_1_MAXTEMP 275
#define HEATER_2_MAXTEMP 275
#define BED_MAXTEMP 150
#define PIDTEMP
#define BANG_MAX 255 // limits current to nozzle while in bang-bang mode; 255=full current
#define PID_MAX 255 // limits current to nozzle while PID is active (see PID_FUNCTIONAL_RANGE below); 255=full current
  #define PID_FUNCTIONAL_RANGE 10 // If the temperature difference between the target temperature and the actual temperature
  #define PID_INTEGRAL_DRIVE_MAX 255  //limit for the integral term
  #define K1 0.95 //smoothing factor within the PID
  #define PID_dT ((16.0 * 8.0)/(F_CPU / 64.0 / 256.0)) //sampling period of the temperature routine
    #define  DEFAULT_Kp 22.2
    #define  DEFAULT_Ki 1.08
    #define  DEFAULT_Kd 114
#define MAX_BED_POWER 255 // limits duty cycle to bed; 255=full current
#define PREVENT_DANGEROUS_EXTRUDE
#define PREVENT_LENGTHY_EXTRUDE
#define EXTRUDE_MINTEMP 170
#define EXTRUDE_MAXLENGTH (X_MAX_LENGTH+Y_MAX_LENGTH) //prevent extrusion of very large distances.
#define ENDSTOPPULLUPS // Comment this out (using // at the start of the line) to disable the endstop pullup resistors
  #define ENDSTOPPULLUP_XMAX
  #define ENDSTOPPULLUP_YMAX
  #define ENDSTOPPULLUP_ZMAX
  #define ENDSTOPPULLUP_XMIN
  #define ENDSTOPPULLUP_YMIN
  #define ENDSTOPPULLUP_ZMIN
const bool X_MIN_ENDSTOP_INVERTING = false; // set to true to invert the logic of the endstop.
const bool Y_MIN_ENDSTOP_INVERTING = false; // set to true to invert the logic of the endstop.
const bool Z_MIN_ENDSTOP_INVERTING = false; // set to true to invert the logic of the endstop.
const bool X_MAX_ENDSTOP_INVERTING = false; // set to true to invert the logic of the endstop.
const bool Y_MAX_ENDSTOP_INVERTING = false; // set to true to invert the logic of the endstop.
const bool Z_MAX_ENDSTOP_INVERTING = false; // set to true to invert the logic of the endstop.
#if defined(COREXY) && !defined(DISABLE_MAX_ENDSTOPS)
  #define DISABLE_MAX_ENDSTOPS
#endif
#define X_ENABLE_ON 0
#define Y_ENABLE_ON 0
#define Z_ENABLE_ON 0
#define E_ENABLE_ON 0 // For all extruders
#define DISABLE_X false
#define DISABLE_Y false
#define DISABLE_Z false
#define DISABLE_E false // For all extruders
#define INVERT_X_DIR false    // for Mendel set to false, for Orca set to true
#define INVERT_Y_DIR false    // for Mendel set to true, for Orca set to false
#define INVERT_Z_DIR false    // for Mendel set to false, for Orca set to true
#define INVERT_E0_DIR false   // for direct drive extruder v9 set to true, for geared extruder set to false
#define INVERT_E1_DIR false   // for direct drive extruder v9 set to true, for geared extruder set to false
#define INVERT_E2_DIR false   // for direct drive extruder v9 set to true, for geared extruder set to false
#define X_HOME_DIR 1
#define Y_HOME_DIR 1
#define Z_HOME_DIR 1
#define min_software_endstops true // If true, axis won't move to coordinates less than HOME_POS.
#define max_software_endstops true  // If true, axis won't move to coordinates greater than the defined lengths below.
#define X_MAX_POS 90
#define X_MIN_POS -90
#define Y_MAX_POS 90
#define Y_MIN_POS -90
#define Z_MAX_POS MANUAL_Z_HOME_POS
#define Z_MIN_POS 0
#define X_MAX_LENGTH (X_MAX_POS - X_MIN_POS)
#define Y_MAX_LENGTH (Y_MAX_POS - Y_MIN_POS)
#define Z_MAX_LENGTH (Z_MAX_POS - Z_MIN_POS)
#define MANUAL_HOME_POSITIONS  // If defined, MANUAL_*_HOME_POS below will be used
#define MANUAL_X_HOME_POS 0
#define MANUAL_Y_HOME_POS 0
#define MANUAL_Z_HOME_POS 205  // For delta: Distance between nozzle and print surface after homing.
#define AUTOLEVEL_GRID 24  // Distance between autolevel Z probing points, should be less than print surface radius/3.
#define NUM_AXIS 4 // The axis order in all axis related arrays is X, Y, Z, E
#define HOMING_FEEDRATE {200*60, 200*60, 200*60, 0}  // set the homing speeds (mm/min)
#define Z_PROBE_OFFSET {0, 19, -8, 0}  // X, Y, Z, E distance between hotend nozzle and deployed bed leveling probe.
#define DEFAULT_AXIS_STEPS_PER_UNIT   {100, 100, 100, 100}
#define DEFAULT_MAX_FEEDRATE          {200, 200, 200, 200}    // (mm/sec)
#define DEFAULT_MAX_ACCELERATION      {9000,9000,9000,9000}    // X, Y, Z, E maximum start speed for accelerated moves. E default values are good for skeinforge 40+, for older versions raise them a lot.
#define DEFAULT_ACCELERATION          3000    // X, Y, Z and E max acceleration in mm/s^2 for printing moves
#define DEFAULT_RETRACT_ACCELERATION  3000   // X, Y, Z and E max acceleration in mm/s^2 for retracts
#define DEFAULT_XYJERK                20.0    // (mm/sec)
#define DEFAULT_ZJERK                 20.0    // (mm/sec)
#define DEFAULT_EJERK                 20.0    // (mm/sec)
#define PLA_PREHEAT_HOTEND_TEMP 180
#define PLA_PREHEAT_HPB_TEMP 70
#define PLA_PREHEAT_FAN_SPEED 255   // Insert Value between 0 and 255
#define ABS_PREHEAT_HOTEND_TEMP 240
#define ABS_PREHEAT_HPB_TEMP 100
#define ABS_PREHEAT_FAN_SPEED 255   // Insert Value between 0 and 255
#define SDSUPPORT // Enable SD Card Support in Hardware Console
#define SOFT_PWM_SCALE 0
#include "Configuration_adv.h"
#include "thermistortables.h"

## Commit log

2014-02-09 Load all STLs (RP) and .DXF/.SVG (Lasercut)
    [bracket_depth_gauge.STL, bracket_groove_mount_dual_he.DXF, bracket_groove_mount_dual_he_slop.DXF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]
2014-02-09 BOM update and laser file update
    [cossel_bom.xlsm]
2014-02-09 Removed old laser file
2014-02-10 Dir rename and file name corrections
    [bracket_depth_gauge.STL, bracket_snsr.STL, bracket_snsr_r4.STL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]
2014-02-18 Added Configuration.h
    [Configuration.h]
